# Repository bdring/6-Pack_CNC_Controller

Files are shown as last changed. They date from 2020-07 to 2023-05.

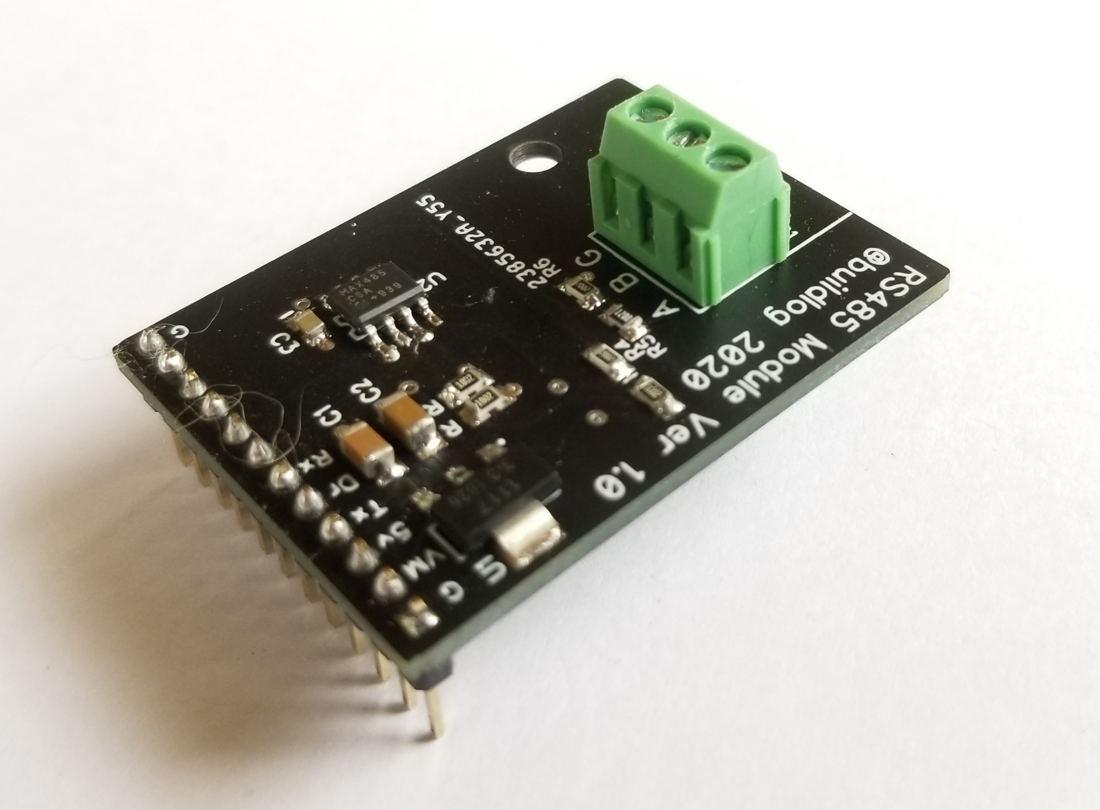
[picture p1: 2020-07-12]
images/20200711_132149.jpg

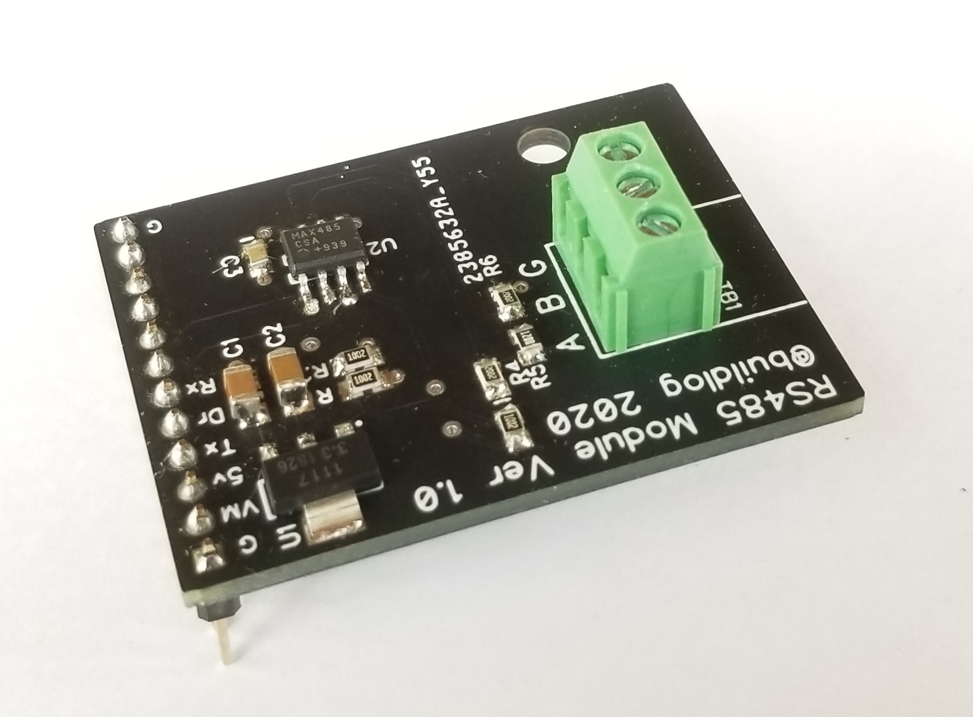
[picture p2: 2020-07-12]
images/20200711_133020.jpg

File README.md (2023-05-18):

# 6-Pack Grbl_ESP32 CNC Controller





### Overview

This is a fully modular CNC controller that runs Grbl_ESP32 firmware.

### Current Source Files.

The latest versions are [now on OSHLabs](https://oshwlab.com/bdring?tab=project&page=1) with the free version of EasyEDA. I did this to make it more accessible and easier to order.

### Features

- ESP32 Sockets to fit both narrow and wide 2 x 19 pin types.
- (6) Stepper Driver Outputs. These can be used for 6 axes (XYZABC) or any (2) can be ganged to allow dual motors on a single axis. These ganged motors can be controlled independently for axis squaring. It supports these types of drivers. Each driver has an independent enable/disable pin.
  - Standard Pololu/StepStick style driver modules.
  - Trinamic SPI type drivers. These are the ultra quiet types with sensorless endstop capability.
  - External Driver with 5V opto isolators.
(5) CNC I/O Modules. These interface with your machine. They include, but are not limited to, siwtch inputs, spindle control and accessory control. Currently there are (5) modules available.
  - High current AC/DC relay
  - 4x 5V Buffered output for lasers, PWM, spindle direction, spindle enable, ect.
  - RS485 Modbus Spindles
  - 0-10V Output Spindles
  - 4x Switch input with Optocouplers, filtering and Schmitt triggers. 
- SD Card Socket
- JTAG Programming/Debugging connector (or access to addition I/O pins

[](https://www.tindie.com/products/33366583/6-pack-universal-cnc-controller/)

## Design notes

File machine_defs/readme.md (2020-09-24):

These machine definitions are for reference only. They are not actively maintained, so they may not compile in future versions of Grbl_ESP32.

Machine definitions in the main Grbl_ESP32 repo are maintained and can be used as a reference to fix problems. You can also ask for help on Slack.

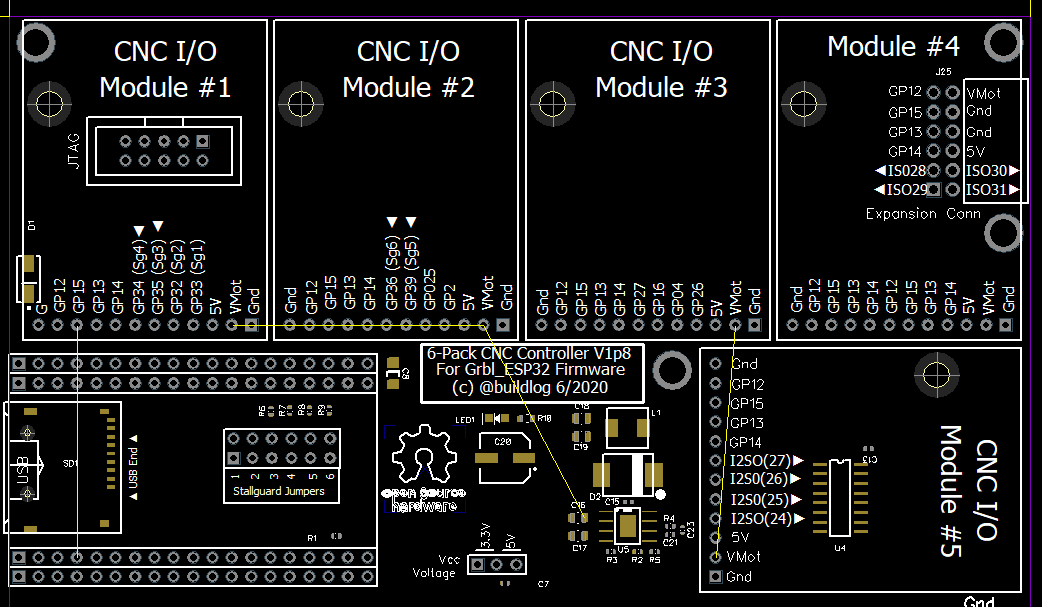
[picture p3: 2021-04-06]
images/expansion_port_pinout.png

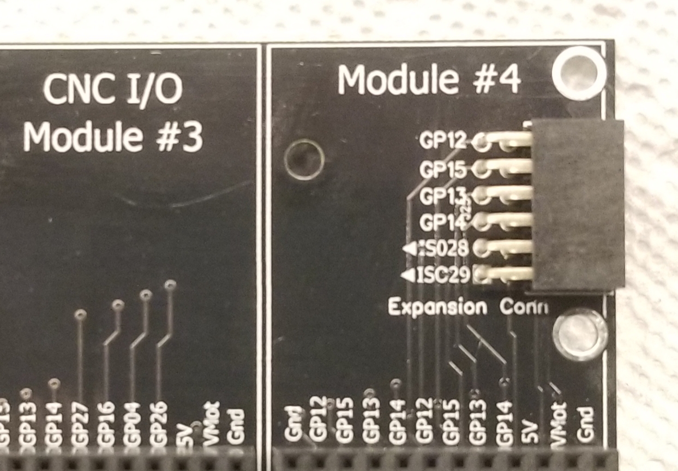
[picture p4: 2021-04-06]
images/6_pack_expansion.jpg

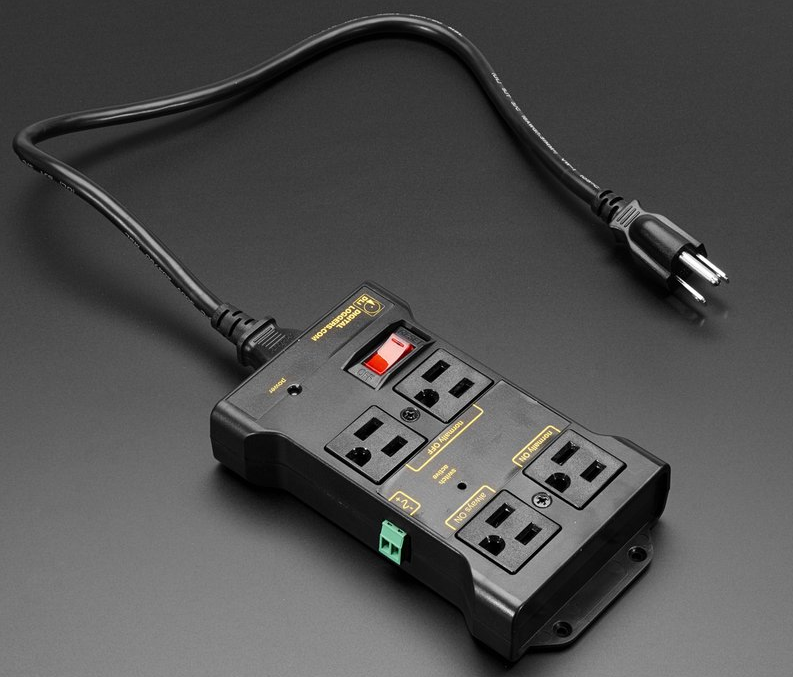
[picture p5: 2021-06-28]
images/iot_relay.png

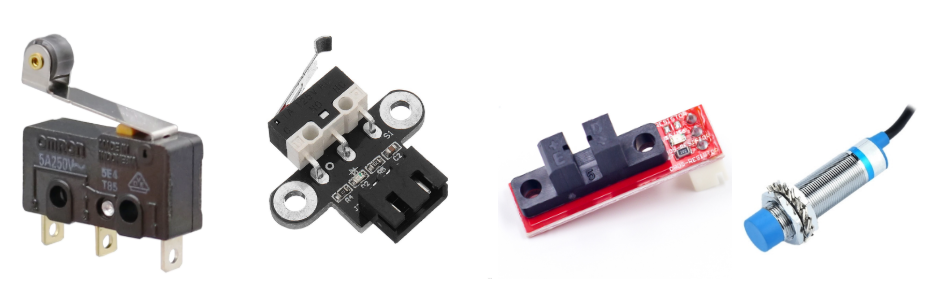
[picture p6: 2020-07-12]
images/switch_types.png

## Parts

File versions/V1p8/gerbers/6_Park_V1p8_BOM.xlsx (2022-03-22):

RefDes | Value | Name | Quantity | SMT | TH | Manufacturer | MFG P/N | Source
C1, C2, C3, C4, C5, C6, C7, C9, C11, C13, C15 | 100nF | NP_100nF_50V_0402 | 11 | 11 |  | Samsung Electro-Mechanics | CL05B104KB54PNC | https://lcsc.com/product-detail/Others_Samsung-Electro-Mechanics_CL05B104KB54PNC_Samsung-Electro-Mechanics-CL05B104KB54PNC_C307331.html
C8 | Do Not Place | NP_DNP_1206 |  |  |  | DNP | DN
C10, C12, C14, C22, C24, C25 | 330uF | POL_330uF_50V_10x10 | 6 | 6 |  | KS | UT1H331M1010VG | https://lcsc.com/product-detail/Aluminum-Electrolytic-Capacitors-SMD_KS-UT1H331M1010VG_C963258.html
C16, C17 | 2.2uF 50V | NP_2.2uF_50V_0805 | 2 | 2 |  | Guangdong Fenghua Advanced Tech | 0805F225M500NT | https://lcsc.com/product-detail/Multilayer-Ceramic-Capacitors-MLCC-SMD-SMT_FH-Guangdong-Fenghua-Advanced-Tech-0805F225M500NT_C49217.html
C18, C19 | 47uF 6.3V | NP_47uF_6.3V_0805 | 2 | 2 |  | Samsung Electro-Mechanics | CL21A476MQYNNNE | https://lcsc.com/product-detail/Multilayer-Ceramic-Capacitors-MLCC-SMD-SMT_SAMSUNG_CL21A476MQYNNNE_47uF-476-20-6-3V_C16780.html
C20 | 100uF 16V | POL_100uF_16V_6.3x5.4 | 1 | 1 |  | ROQANG | RT1C101M0605 | https://lcsc.com/product-detail/Aluminum-Electrolytic-Capacitors-SMD_ROQANG-RT1C101M0605_C267461.html
C21 | 39pF 50V | NP_39pF_50V_0402 | 1 | 1 |  | Yageo | CC0402JRNPO9BN390 | https://lcsc.com/product-detail/Multilayer-Ceramic-Capacitors-MLCC-SMD-SMT_39pF-390-5-50V_C106223.html/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
C23 | 6.8nF 50V | NP_6.8nF_50V_0402 | 1 | 1 |  | Guangdong Fenghua Advanced Tech | 0402B682K500NT | https://lcsc.com/product-detail/Multilayer-Ceramic-Capacitors-MLCC-SMD-SMT_6-8nF-682-10-50V_C1542.html
D1 | 40V 3A | Schottkey_40V_3A_DO-214AC | 1 | 1 |  | MDD（Microdiode Electronics） | B340A | https://lcsc.com/product-detail/Schottky-Barrier-Diodes-SBD_Jiangsu-Yutai-Elec-B340A_C64982.html
D2 | B560C | B560C | 1 | 1 |  | Diodes Incorporated | B560C-13-F | https://lcsc.com/product-detail/Schottky-Barrier-Diodes-SBD_Diodes-Incorporated-B560C-13-F_C85100.html
J1, J8, J12, J15, J19, J26 | 2 Pos | HDR Socket 1x2 0.1 | 6 |  | 6 | BOOMELE(Boom Precision Elec) | C49661 | https://lcsc.com/product-detail/Pin-Header-Female-Header_BOOMELE-Boom-Precision-Elec-C49661_C49661.html
J2, J3, J9, J10, J13, J14, J16, J17, J20, J21, J27, J28 | 8S | HDR Socket 1x8 0.1 | 12 |  | 12 | BOOMELE(Boom Precision Elec) | C27438 | https://lcsc.com/product-detail/Female-Header_2-54mm-1-8P-Straight-Female-header_C27438.html
J4, J5, J6, J7 | 19S | HDR Socket 1x19 0.1 | 4 |  | 4 | BOOMELE(Boom Precision Elec) | C319202 | https://lcsc.com/product-detail/Lack-of-specifications_BOOMELE-Boom-Precision-Elec-C319202_C319202.html
J11 | Do Not Place | DC3-10P
J18 | 6S | HDR Pin 2x6 0.1 | 1 |  | 1 | MINTRON | MTP125-1206S1 | https://lcsc.com/product-detail/Pin-Header-Female-Header_MINTRON-MTP125-1206S1_C358695.html
J22, J23, J24 | 3P | HDR Pin 1x3 0.1 | 3 |  | 3 | BOOMELE(Boom Precision Elec) | C49257 | https://lcsc.com/product-detail/Pin-Header-Female-Header_BOOMELE-Boom-Precision-Elec-C49257_C49257.html
J25 | Do Not Place | Header_2x6S_RA |  |  | 1
JP1, JP2, JP3, JP4 | 3P | Jumper_3p | 4 |  | 4 | BOOMELE(Boom Precision Elec) | C49257 | https://lcsc.com/product-detail/Pin-Header-Female-Header_BOOMELE-Boom-Precision-Elec-C49257_C49257.html
L1 | 10uH | 10uH_SMD_5.2x5.4 | 1 | 1 |  | Sunlord | MWSA0503S-100MT | https://lcsc.com/product-detail/Power-Inductors_Sunlord-MWSA0503S-100MT_C408412.html
LED1 | GRN | LED_GRN_0805 (Foshan) | 1 | 1 |  | Foshan NationStar Optoelectronics | NCD0805G1 | https://lcsc.com/product-detail/Light-Emitting-Diodes-LED_Foshan-NationStar-Optoelectronics-NCD0805G1_C84260.html
MH1, MH2, MH3, MH4, MH5, MH6 | Do Not Place | Mounting_hole_M3.7
MOD1, MOD2, MOD3, MOD4, MOD5 | 1x12 Socket | CNC_Module_Socket | 5 |  | 5 | CJT(Changjiang Connectors) | A2541HWV-12P | https://lcsc.com/product-detail/Pin-Header-Female-Header_CJT-Changjiang-Connectors-A2541HWV-12P_C225509.html
R1, R6, R7, R8, R9 | 10k | 10k_0402 | 5 | 5 |  | YAGEO | RC0402FR-0710KL | https://lcsc.com/product-detail/Chip-Resistor-Surface-Mount_YAGEO-RC0402FR-0710KL_C60490.html
R2 | 270k | 270k_0402 | 1 | 1 |  | Uniroyal Elec | 0402WGF2703TCE | https://lcsc.com/product-detail/Chip-Resistor-Surface-Mount_Uniroyal-Elec-0402WGF2703TCE_C25770.html/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
R3 | 100k | 100k_0402 | 1 | 1 |  | Uniroyal Elec | 0402WGF1003TCE | https://lcsc.com/product-detail/Chip-Resistor-Surface-Mount_Uniroyal-Elec-0402WGF1003TCE_C25741.html/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
R4 | 13k | 13k_0402 | 1 | 1 |  | Uniroyal Elec | 0402WGF1302TCE | https://lcsc.com/product-detail/Chip-Resistor-Surface-Mount_UNI-ROYAL-Uniroyal-Elec-0402WGF1302TCE_C25754.html
R5 | 51k | 51k_0402 | 1 | 1 |  | Uniroyal Elec | 0402WGF5102TCE | https://lcsc.com/product-detail/Chip-Resistor-Surface-Mount_Uniroyal-Elec-0402WGF5102TCE_C25794.html/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
R10 | 3.0k | 3.0k_0603 | 1 | 1 |  | YAGEO | RC0603FR-073KL | https://lcsc.com/product-detail/Chip-Resistor-Surface-Mount_3KR-3001-1_C126358.html
SD1 | Micro SD | TF-01A | 1 | 1 |  | Korean Hroparts Elec | TF-01A | https://lcsc.com/product-detail/Card-Sockets-Connectors_Korean-Hroparts-Elec-TF-01A_C91145.html
TB1, TB2, TB3, TB5, TB6, TB7 | 4 Pos | TB_3p5mm_4POS_KF2EDGR | 6 |  | 6 | Cixi Kefa Elec | KF2EDGR-3.5-4P | https://lcsc.com/product-detail/Pluggable-System-Terminal-Block_Cixi-Kefa-Elec-KF2EDGR-3-5-4P_C441173.html
TB4 | 2 Pos | TB_5mm_2POS Socket | 1 |  | 1 | Ningbo Xinlaiya Elec. | XY2500R-B-5.00-2P | https://lcsc.com/product-detail/Pluggable-System-Terminal-Block_Ningbo-Xinlaiya-Elec-XY2500R-B-5-00-2P_C505815.html
U1, U2, U3, U4 | 74AHCT595 | 74AHCT595 | 4 | 4 |  | Texas Instruments | SN74AHCT595DR | https://lcsc.com/product-detail/74-Series_Texas-Instruments_SN74AHCT595DR_Texas-Instruments-Texas-Instruments-SN74AHCT595DR_C133793.html
U5 | TPS54360 | TPS54360DDAR | 1 | 1 |  | Texas Instruments | TPS54360DDAR | https://lcsc.com/product-detail/DC-DC-Converters_Texas-Instruments-Texas-Instruments-TPS54360DDAR_C44377.html
 |  | Total parts | 86 | 44 | 43
 |  | Unique count | 29 | 20 | 10

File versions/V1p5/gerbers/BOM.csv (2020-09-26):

RefDes | Value | Name | Quantity | Manufacturer | MFG P/N
C1, C2, C3, C4, C5, C6, C7, C9, C11, C13, C16 | 100nF | NP_100nF_50V_0805 | 11 | KEMET | C0805C104K5RACAUTO
C8 | DNP | NP_DNP_1206 | 1 | DNP | DN
C10, C12, C15, C21, C23, C24 | 330uF | POL_330uF_50V_10x10 | 6 | Lelon | VZT331M1HTR-1010
C14, C19 | 10uF 35V | NP_10uF_35V_1206 | 2 | Taiyo Yuden | GMK316BJ106KL-T
C17 | 10uF | NP_10uF_50V_1206 | 1 | Taiyo Yuden | UMK316BBJ106ML-T
C18 | 100uF 16V | POL_100uF_16V_6.3x5.4 | 1 | PANASONIC | EEEHAC101WAP
C20 | 22uF | NP_22uF_6.3V_1206 | 1 | Taiyo Yuden | JMK316BJ226KL-T
C22 | 3.3nF | NP_3.3nF_50V_0603 | 1 | YAGEO | CS0603KRX7R9BB332
D1 | 40V 3A | Schottkey_40V_3A_DO-214AC | 1 | MDD(Microdiode Electronics) | B340A
J1, J8, J12, J15, J19, J25 |  | HDR Socket 1x2 0.1 | 6 | BOOMELE(Boom Precision Elec) | C49661
J2, J3, J9, J10, J13, J14, J16, J17, J20, J21, J26, J27 |  | HDR Socket 1x8 0.1 | 12 | BOOMELE(Boom Precision Elec) | C27438
J4, J5, J6, J7 |  | HDR Socket 1x19 0.1 | 4 | Popular Products About LCSC | C319202
J11 | JTAG | DC3-10P | 1
J18 |  | HDR Pin 2x6 0.1 | 1 | MINTRON | MTP125-1206S1
J22, J23, J24 |  | HDR Pin 1x3 0.1 | 3 | BOOMELE(Boom Precision Elec) | C49257
JP1, JP2, JP3, JP4 |  | Jumper_3p | 4 | BOOMELE(Boom Precision Elec) | C49257
L1 | 5.6uH | 5.6uH_SMD_10.0_11.5 | 1 | COILMX | MS1040-5R6M
LED1 | GRN | LED_GRN_0805 (Foshan) | 1 | Foshan NationStar Optoelectronics | NCD0805G1
MH1, MH2, MH3, MH4 |  | Mounting_hole_M3.7 | 4
MOD1, MOD2, MOD3, MOD4, MOD5 | 1x12 Socket | CNC_Module_Socket | 5 | CJT(Changjiang Connectors) | A2541HWV-12P
R1 | 115k | 115K_0603 | 1 | YAGEO | RC0603FR-07115KL
R2 | 22.1k | 22.1k_0603 | 1 | YAGEO | RC0603FR-0722K1L
R3 | 200k | 200k_0603 | 1 | YAGEO | RC0603FR-07200KL
R4 | 42.1k | 41.2k_0603 | 1 | YAGEO | RC0603FR-0741K2L
R5, R6, R7, R8 | 10k | 10k_0805 | 4 | YAGEO | RC0805FR-0710KL
R9 | 3.0k | 3.0k_0805 | 1 | YAGEO | RC0805FR-073KL
SD1 | Micro SD | TF-01A | 1 | Korean Hroparts Elec | TF-01A
TB1, TB2, TB3, TB5, TB6, TB7 | 4 Pos | TB_3.5mm_4POS_PHOENIX_1945119 | 6 | Phoenix contact | 1945119 (Mate is 1984183)
TB4 | 2 Pos | TB_5mm_2POS Socket | 1 | Ningbo Xinlaiya Elec. | XY2500R-B-5.00-2P (Mate is XY2500F-A-5.0-2P)
U1, U2, U3, U4 | 74AHCT595 | 74AHCT595 | 4 | Nexperia | 74AHCT595D,118
U5 | AP64350SP-13 | AP64350 | 1 | Diodes Inc | AP64350SP-13

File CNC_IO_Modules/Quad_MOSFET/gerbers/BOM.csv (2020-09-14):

RefDes | Value | Name | Quantity | Manufacturer | MFG P/N
LED1, LED2, LED3, LED4 | GRN | LED_GRN_0805 | 4 | Lite-On | LTST-C170KGKT
MOD1 | 1x12 P | CNC_Module_Pins | 1 | CJT(Changjiang Connectors) | A2541WV-12P
Q1, Q2, Q3, Q4 | 42V 10A | NCV8403A | 4 | On Semiconductor | NCV8403A
R1, R2, R3, R4 | 300R | 300R_0603 | 4 | YAGEO | RC0603FR-07330RL
R5 | 10R | 10R_0805 | 1 | YAGEO | RC0805FR-0710RL
TB1 | 8 Pos | TB_3p5mm_8POS_PHOENIX_1945151 | 1 | Phoenix contact | 1945151
TB2 | 2 Pos | TB_3.5mm_2POS_SOCKET_VERT | 1 | Ningbo Xinlaiya Elec | XY2500R-B-5.00-2P

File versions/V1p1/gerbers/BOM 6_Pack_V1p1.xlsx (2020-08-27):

RefDes | Quantity | Qty SMT | Qty TH | Name | Value | Manufacturer | Mfg P/N | Source
C1, C2 | 2 | 2 |  | Capacitor 1206 | 10uF | Taiyo Yuden | GMK316BJ106KL-T | https://lcsc.com/product-detail/Multilayer-Ceramic-Capacitors-MLCC-SMD-SMT_Taiyo-Yuden-GMK316BJ106KL-T_C92797.html
C3, C6, C7, C13, C14, C23, C24, C25, C26, C27, C28 | 11 | 11 |  | Capacitor 0805 | 100nF | Kemet | C0805C104K5RACAUTO | https://lcsc.com/product-detail/Multilayer-Ceramic-Capacitors-MLCC-SMD-SMT_KEMET_C0805C104K5RACAUTO_100nF-104-10-50V-Car-level_C129641.html
C4 | 1 | 1 |  | Capacitor 0805 | 150pF | CCTC | TCC0805X7R151K500BT | https://lcsc.com/product-detail/Multilayer-Ceramic-Capacitors-MLCC-SMD-SMT_CCTC-TCC0805X7R151K500BT_C282743.html
C5, C9 | 2 | 2 |  | Capacitor 1206 | 22uF 6.3V | Taiyo Yuden | JMK316BJ226KL-T | https://lcsc.com/product-detail/Multilayer-Ceramic-Capacitors-MLCC-SMD-SMT_TAIYO-YUDEN_JMK316BJ226KL-T_22uF-226-10-6-3V_C92791.html
C8 | 1 | 1 |  | Capacitor, Electrolytic | 100u 16V | Panasonic | EEEHAC101WAP | https://lcsc.com/product-detail/Aluminum-Electrolytic-Capacitors-SMD_PANASONIC-EEEHAC101WAP_C336467.html
C17, C18, C19, C20, C21, C22 | 6 | 6 |  | Capacitor, Electrolytic | 330uF 50V | Lelon | VZT331M1HTR-1010 | https://lcsc.com/product-detail/Others_Lelon-VZT331M1H1010-TRO_C249985.html
D1, D2 | 2 | 2 |  | Diode, Schottkey 3A DO-214AC | 3A | (MDD) Jiangsu Yutai Elec | C64982 | https://lcsc.com/product-detail/Schottky-Barrier-Diodes-SBD_Jiangsu-Yutai-Elec-B340A_C64982.html
J1, J3, J6,J9 | 4 |  | 4 | 1x19 Female Header 0.1 |  | AliExpress |  | https://www.aliexpress.com/item/100Pcs-Per-Lot-2-54mm-Pitch-1x19-Pin-19-Pin-Female-Single-Row-Straight-Header-Strip/32760221364.html
J4, J5, J8, JP1, JP2, JP3, JP4 | 7 |  | 7 | Header, Male 1x3 0.1 | 1x3 | Boom Precision Elec | C49257 | https://lcsc.com/product-detail/Pin-Header-Female-Header_BOOMELE-Boom-Precision-Elec-C49257_C49257.html
J12 | 1 |  | 1 | Header, Male 2x6 | 2x6 | MINTRON | MTP125-1206S1 | https://lcsc.com/product-detail/Pin-Header-Female-Header_MINTRON-MTP125-1206S1_C358695.html
J14, J15, J16, J17, J18, J19, J26, J27, J28, J29, J30, J31 | 12 |  | 12 | Header, Female 1x8 | 1x8 | BOOMELE(Boom Precision Elec) | C27438 | https://lcsc.com/product-detail/Female-Header_2-54mm-1-8P-Straight-Female-header_C27438.html
J20, J21, J22, J23, J24, J25 | 6 |  | 6 | Header, Female 1x2 | 1x2 | BOOMELE(Boom Precision Elec) | C49661 | https://lcsc.com/product-detail/Pin-Header-Female-Header_BOOMELE-Boom-Precision-Elec-C49661_C49661.html
J33 | 0 |  |  | Do not place
L1 | 1 | 1 |  | Inductor | 4.7uH | Chilisin Elec | MHCI06030-4R7M-R8 | https://lcsc.com/product-detail/Power-Inductors_Chilisin-Elec-MHCI06030-4R7M-R8_C108295.html
LED1 | 1 | 1 |  | LED Clear Green 0805 |  | Foshan NationStar Optoelectronics | NCD0805G1 | https://lcsc.com/product-detail/Light-Emitting-Diodes-LED_Emerald-SMDLED-Iv-220-270mcd-atIF-5mA_C84260.html
MOD1, MOD2, MOD3, MOD4, MOD5 | 5 |  | 5 | Header, Feamle 1x12 | 1x12 | HOAUC | 2685Y-112CNG1SNA01 | https://lcsc.com/product-detail/Pin-Header-Female-Header_HOAUC-2685Y-112CNG1SNA01_C350303.html
R1, R2 | 2 | 2 |  | RES_0805 | 100k | YAGEO | AC0805FR-07100KL | https://lcsc.com/product-detail/Chip-Resistor-Surface-Mount_100KR-1003-1_C144587.html
R3 | 1 | 1 |  | RES_0805 | 40.2k | YAGEO | AC0805FR-0740K2L | https://lcsc.com/product-detail/Others_YAGEO-AC0805FR-0740K2L_C228820.html
R4 | 1 | 1 |  | RES_0805 | 210k | YAGEO | AC0805FR-07210KL | https://lcsc.com/product-detail/Others_YAGEO-AC0805FR-07210KL_C228629.html
R5, R6, R7, R8 | 4 | 4 |  | RES_0805 | 10k | YAGEO | AC0805FR-0710KL | https://lcsc.com/product-detail/Chip-Resistor-Surface-Mount_10KR-1002-1_C140868.html
R10 | 1 | 1 |  | RES_0805 | 300R | YAGEO | RC0805FR-07300RL | https://lcsc.com/product-detail/Chip-Resistor-Surface-Mount_300R-300R-1_C114529.html
SD1 | 1 | 1 |  | TF-01A |  | Korean Hroparts Elec TF-01A | TF-01A | https://lcsc.com/product-detail/Connector-Card-Sockets_Korean-Hroparts-Elec-TF-01A_C91145.html
TB1 | 1 |  | 1 | 2 Pos Terminal Block |  | Ningbo Xinlaiya Elec. | XY2500R-B-5.00-2P | https://lcsc.com/product-detail/Pluggable-System-Terminal-Block_Ningbo-Xinlaiya-Elec-XY2500R-B-5-00-2P_C505815.html
TB2, TB3, TB4, TB5, TB6, TB7 | 0 |  |  | 4 Pos Terminal Block |  | Phoenix Contact | 1945119 | https://www.mouser.com/ProductDetail/Phoenix-Contact/1945119?qs=BYlwlsDsB%2FoxVFDUDE1oIQ%3D%3D
U1 | 1 | 1 |  | Power Supply, Buck 3A | 3A | Monolithic Power Systems | MP1584EN-LF-Z | https://lcsc.com/product-detail/DC-DC-Converters_MPS_MP1584EN-LF-Z_MP1584EN-LF-Z_C15051.html
U2, U3, U4, U5 | 4 | 4 |  | 74AHCT595 | 74AHCT595 | Nexperia | 74AHCT595D,118 | https://www.mouser.com/ProductDetail/Nexperia/74AHCT595D118?qs=P62ublwmbi%2FjQEpjzH34Ig%3D%3D
Totals | 65 | 29 | 36

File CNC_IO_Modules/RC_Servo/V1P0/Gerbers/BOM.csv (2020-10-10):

RefDes | Value | Name | Quantity | Manufacturer | MFG P/N | Source
J1, J2, J3, J4 | 1x3 | HDR Pin 1x3 0.1 | 4 | BOOMELE(Boom Precision Elec) | C49257 | https://lcsc.com/product-detail/Pin-Header-Female-Header_BOOMELE-Boom-Precision-Elec-C49257_C49257.html
MOD1 | 1x12 P | CNC_Module_Pins | 1 | CJT(Changjiang Connectors) | A2541WV-12P | https://lcsc.com/product-detail/Pin-Header-Female-Header_CJT-Changjiang-Connectors-A2541WV-12P_C225487.html
S1 | SPDT | XKB_SS-12D11L5 | 1 | XKB Connectivity | SS-12D11L5 | https://lcsc.com/product-detail/Toggle-Switches_XKB-Connectivity-SS-12D11L5_C319010.html
TB4 | 2 Pos | TB_5mm_2POS Socket | 1 | Ningbo Xinlaiya Elec. | XY2500R-B-5.00-2P | https://lcsc.com/product-detail/Pluggable-System-Terminal-Block_Ningbo-Xinlaiya-Elec-XY2500R-B-5-00-2P_C505815.html

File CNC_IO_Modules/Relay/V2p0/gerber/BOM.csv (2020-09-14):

RefDes | Value | Name | Quantity | Manufacturer | MFG P/N | Source
D1 |  | Schottkey_40V_3A_DO-214AC | 1 | MDD(Microdiode Electronics) | B340A | https://lcsc.com/product-detail/Schottky-Barrier-Diodes-SBD_Jiangsu-Yutai-Elec-B340A_C64982.html
K1 | 5VDC | Relay_SRD-05VDC-SL-C | 1 |  | SRD-05VDC-SL-C | https://lcsc.com/product-detail/Relays_Ningbo-Songle-Relay-SRD-05VDC-SL-C_C35449.html
LED1 | GRN | LED_GRN_0805 (Foshan) | 1 | Foshan NationStar Optoelectronics | NCD0805G1 | https://lcsc.com/product-detail/Light-Emitting-Diodes-LED_Foshan-NationStar-Optoelectronics-NCD0805G1_C84260.html
MOD1 | 1x12 P | CNC_Module_Pins | 1 | CJT(Changjiang Connectors) | A2541WV-12P | https://lcsc.com/product-detail/Pin-Header-Female-Header_CJT-Changjiang-Connectors-A2541WV-12P_C225487.html
Q1 | NPN 100mA 45V | MMBT9014B | 1 | ST(Semtech) | MMBT9014B | https://lcsc.com/product-detail/Transistors-NPN-PNP_ST-Semtech-MMBT9014B_C109430.html
R1 | 1.0k | 1.0k_0805 | 1 | YAGEO | RC0805FR-071K5L | https://lcsc.com/product-detail/Chip-Resistor-Surface-Mount_YAGEO-RC0805FR-071KL_C95781.html
R2 | 1.5k | 1.5k_0805 | 1 | YAGEO | RC0805FR-071K5L | https://lcsc.com/product-detail/Chip-Resistor-Surface-Mount_1-5KR-1501-1_C114555.html
TB2 |  | TB_5mm_3POS | 1 | JILN

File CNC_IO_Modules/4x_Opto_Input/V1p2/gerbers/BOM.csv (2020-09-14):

RefDes | Value | Name | Quantity | Manufacturer | MFG P/N
C1, C2 | 1uF | NP_1uF_50V_0805 | 2 | CCTC | TCC0805X7R105K500DTB
C3 | 2.2uF | NP_2.2uF_16V_0805 | 1 | Samsung Electro-Mechanics | CL21B225KOFNNNE
C4, C5, C6, C7, C8 | 100nF | NP_100nF_50V_0603 | 5 | KEMET | C0603C104K5RACTU
MOD1 |  | CNC_Module | 1 | CJT(Changjiang Connectors) | A2541WV-12P
OPT1 | TP521-4 | TLP521-4 | 1 | Isocom Components | TLP521-4GBSM
PS1 | 5V | B0505S-1WR3 | 1 | MORNSUN Guangzhou S&T | B0505S-1WR3
PS2 | 3.3V | LDO_3V3_150mA_SOT-89 | 1 | Diodes Incorporated | AP2204RA-3.3TRG1
R1, R2, R3, R4 | 300R | 300R_0603 | 4 | YAGEO | RC0603FR-07330RL
R5, R6, R7, R8 | 10k | 10k_0603 | 4 | YAGEO | RC0603FR-0710KL
R9, R10, R11, R12, R13 | 220R | 220R_0603 | 5 | YAGEO | RC0603FR-07220RL
TB1, TB2 |  | KL128H-3.5_3x2 | 2 | KEFA | KF128A-3.5 3P
U2 |  | SN74AC14D | 1 | Texas Instruments | SN74HC14PWR

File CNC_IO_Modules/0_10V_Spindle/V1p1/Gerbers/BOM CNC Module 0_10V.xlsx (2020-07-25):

RefDes | Quantity | Qty SMT | Qty TH | Value | Name | Pattern | Manufacturer | MFG P/N | Source | Alt Source
C1, C2 | 1 | 1 |  | 100nF | CAP_0805 | CAP_0805 | Kemet | C0805C104K5RACAUTO | https://lcsc.com/product-detail/Multilayer-Ceramic-Capacitors-MLCC-SMD-SMT_KEMET_C0805C104K5RACAUTO_100nF-104-10-50V-Car-level_C129641.html
LED1, LED2, LED3, LED4 | 4 | 4 |  | Green | LED Green Clear | 805 | Lite-On | LTST-C170KGKT | https://lcsc.com/product-detail/Light-Emitting-Diodes-LED_Lite-On-LTST-C170KGKT_C98221.html
MOD1 | 1 |  | 0 | Do not place
OPT1, OPT2 | 2 | 2 |  | Opto | Opto | SMD4 | Everlight Elec | EL817S1(D)(TU)-F | https://lcsc.com/product-detail/Optocouplers_Everlight-Elec-EL817S1-D-TU-F_C108319.html
R1, R2, R3, R4, R5 | 5 | 5 |  | 300R | Resistor 300R 1% |  | YAGEO | AC0805FR-07300RL | https://lcsc.com/product-detail/_AC0805FR-07300RL_C144566.html
R6, R9, R10 | 4 | 4 |  | 10k | Resistor 10k 1% | RES_0805 | YAGEO | AC0805FR-0710KL | https://lcsc.com/product-detail/Chip-Resistor-Surface-Mount_10KR-1002-1_C140868.html
R7 | 1 | 1 |  | 20k | Pot 20K SMT | Pot | HDK(Hokuriku Elec Industry) | VG039NCHXTB203 | https://lcsc.com/product-detail/Variable-Resistors_HDK-Hokuriku-Elec-Industry-VG039NCHXTB203_C128550.html
R8 | 1 | 1 |  | 4.99K | Resistor 4.99K 1% 0805 | 805 | YAGEO | AC0805FR-074K99L | https://lcsc.com/product-detail/Others_YAGEO-AC0805FR-074K99L_C228871.html
TB1 | 1 |  | 0 | Do Not Place
U1 | 1 | 1 |  | LM358P | LM358 | SOIC-8 | STMicroelectronics | LM358ADT | https://lcsc.com/product-detail/General-Purpose-Amplifiers_STMicroelectronics-LM358ADT_C92457.html
Total |  | 19

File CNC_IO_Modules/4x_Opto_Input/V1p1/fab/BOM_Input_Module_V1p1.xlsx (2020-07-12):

RefDes | Quantity | Qty SMT | Qty TH | Value | Name | Pattern | Manufacturer | Mfg P/N | Source
C1, C2 | 2 | 2 |  | 1uF | Capacitor 0805 1uF 50V 20% | CAP_0805 | CCTC | TCC0805X7R105K500DTB | https://lcsc.com/product-detail/Multilayer-Ceramic-Capacitors-MLCC-SMD-SMT_CCTC-TCC0805X7R105K500DTB_C282736.html
C3 | 1 | 1 |  | 2.2uF | Capacitor 0805 | CAP_0805 | Samsung Electro-Mechanics | CL21B225KOFNNNE | https://lcsc.com/product-detail/Multilayer-Ceramic-Capacitors-MLCC-SMD-SMT_SAMSUNG_CL21B225KOFNNNE_2-2uF-225-10-16V_C28234.html
C4, C5, C6, C7, C8 | 4 | 4 |  | 100nF | Capacitor 0603 | CAP_0603 | Walsin Tech Corp | 0603F104Z250 | https://lcsc.com/product-detail/Multilayer-Ceramic-Capacitors-MLCC-SMD-SMT_Walsin-Tech-Corp-0603F104Z250_C125841.html
MOD1 | 0 |  |  |  | Header, Male 1x12 0.1" | Do Not Place
OPT1 | 1 | 1 |  | TP521-4 | Optocoupler | TLP521-4SM | Isocom Components | TLP521-4GBSM | https://lcsc.com/product-detail/Optocouplers_Isocom-Components-TLP521-4GBSM_C191332.html
PS1 | 1 |  | 0 | 5V | Isloated P/S 5V/5V | Do Not Place
PS2 | 1 | 1 |  |  | LDO 5V | SOT89 | Diodes Incorporated | AP2204RA-3.3TRG1 | https://lcsc.com/product-detail/Low-Dropout-Regulators-LDO_Diodes-Incorporated-AP2204RA-3-3TRG1_C151625.html
R1, R2, R3, R4 | 4 | 4 |  | 300 | Resitor 0603 | RES_0603 | LIZ Elec | CR0603JA0301G | https://lcsc.com/product-detail/Chip-Resistor-Surface-Mount_LIZ-Elec-CR0603JA0301G_C101323.html
R5, R6, R7, R8 | 4 | 4 |  | 10k | Resitor 0603 | RES_0603 | YAGEO | RC0603FR-0710KL | https://lcsc.com/product-detail/Chip-Resistor-Surface-Mount_10KR-1002-1_C98220.html
R9, R10, R11, R12, R13 | 5 | 5 |  | 220 | Resitor 0603 | RES_0805 | YAGEO | RC0603FR-07220RL | https://lcsc.com/product-detail/Chip-Resistor-Surface-Mount_220R-220R-1_C107696.html
TB1, TB3 | 0 |  | 0 |  | Do not place | Do not place
TB2, TB4 | 0 |  | 0 |  | Do not place | Do not place
U2 | 1 | 1 |  |  | Schmitt Trigger SN74AC14D | TSSOP-14 | Texas Instruments | SN74HC14PWR | https://lcsc.com/product-detail/Gates-and-Inverters_Texas-Instruments_SN74HC14PWR_Texas-Instruments-Texas-Instruments-SN74HC14PWR_C6821.html
 |  | 23

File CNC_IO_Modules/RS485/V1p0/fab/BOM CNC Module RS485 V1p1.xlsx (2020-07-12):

RefDes | Quantity | Qty SMT | Qty TH | Value | Name | Pattern | Manufacturer | MFG P/N | Source
C1 | 1 | 1 |  | 10uF | CAP_NP_1206 | CAP_1206 | Taiyo Yuden | GMK316BJ106KL-T | https://lcsc.com/product-detail/Multilayer-Ceramic-Capacitors-MLCC-SMD-SMT_Taiyo-Yuden-GMK316BJ106KL-T_C92797.html
C2 | 1 | 1 |  | 22uF |  | CAP_1206 | Taiyo Yuden | JMK316BJ226KL-T | https://lcsc.com/product-detail/Multilayer-Ceramic-Capacitors-MLCC-SMD-SMT_TAIYO-YUDEN_JMK316BJ226KL-T_22uF-226-10-6-3V_C92791.html
C3 | 1 | 1 |  | 100nF | CAP_0805 | CAP_0805 | Kemet | C0805C104K5RACAUTO | https://lcsc.com/product-detail/Multilayer-Ceramic-Capacitors-MLCC-SMD-SMT_KEMET_C0805C104K5RACAUTO_100nF-104-10-50V-Car-level_C129641.html
MOD1 | 1 |  | 0 |  | Do not place
R1, R2, R3 | 3 | 3 |  | 10k | RES_0805 | RES_0805 | YAGEO | AC0805FR-0710KL | https://lcsc.com/product-detail/Chip-Resistor-Surface-Mount_10KR-1002-1_C140868.html
R4, R6 | 2 | 2 |  | 20k | RES_0805 | RES_0805 | YAGEO | RC0805FR-0720KL | https://lcsc.com/product-detail/Chip-Resistor-Surface-Mount_20KR-2002-1_C114566.html
R5 | 1 | 1 |  | 120 | RES_0805 | RES_0805 | YAGEO | RC0805FR-07120RL | https://lcsc.com/product-detail/Chip-Resistor-Surface-Mount_120R-120R-1_C114245.html
TB1 | 1 |  | 0 |  | Do Not Place
U1 | 1 | 1 |  | 3.3V | AMS1117 | SOT223-4 | Advanced Monolithic Systems | AMS1117-3.3 | https://lcsc.com/product-detail/Low-Dropout-Regulators-LDO_AMS_AMS1117-3-3_AMS1117-3-3_C6186.html
U2 | 1 | 1 |  |  | MAX485CSA | SOIC-8/150mil | Maxim Integrated | MAX3485ESA+T | https://lcsc.com/product-detail/RS-485-RS-422-ICs_Maxim-Integrated_MAX3485ESA-T_Maxim-Integrated-MAX3485ESA-T_C18148.html
Total |  | 11

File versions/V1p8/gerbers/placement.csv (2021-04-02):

RefDes | Origin X (mm) | Origin Y (mm) | Side | Rotate
C1 | 39.85 | 60.173 | Top | 0.0
C2 | 30.111 | 60.649 | Top | 0.0
C3 | 51.701 | 60.649 | Top | 0.0
C4 | 70.751 | 60.649 | Top | 0.0
C5 | 92.341 | 60.649 | Top | 0.0
C6 | 110.099 | 60.649 | Top | 0.0
C7 | 74.995 | 67.634 | Top | 180.0
C8 | 60.332 | 95.098 | Top | 270.0
C9 | 78.585 | 60.173 | Top | 0.0
C10 | 26.518 | 53.243 | Top | 90.0
C11 | 116.368 | 60.173 | Top | 0.0
C12 | 48.108 | 53.243 | Top | 90.0
C13 | 122.72 | 85.256 | Top | 0.0
C14 | 67.158 | 53.243 | Top | 90.0
C15 | 91.193 | 78.271 | Top | 0.0
C16 | 84.621 | 76.207 | Top | 0.0
C17 | 84.621 | 73.825 | Top | 0.0
C18 | 85.097 | 89.224 | Top | 0.0
C19 | 85.097 | 86.843 | Top | 0.0
C20 | 75.095 | 83.985 | Top | 180.0
C21 | 96.686 | 73.984 | Top | 180.0
C22 | 88.748 | 53.243 | Top | 90.0
C23 | 98.273 | 74.619 | Top | 90.0
C24 | 106.528 | 53.243 | Top | 90.0
C25 | 127.642 | 53.243 | Top | 90.0
D1 | 12.548 | 107.48 | Top | 90.0
D2 | 91.193 | 81.763 | Top | 180.0
J1 | 22.708 | 44.298 | Top | 180.0
J2 | 18.898 | 35.408 | Top | 270.0
J3 | 31.598 | 35.408 | Top | 270.0
J4 | 34.138 | 96.368 | Top | 0.0
J5 | 34.138 | 93.828 | Top | 0.0
J6 | 34.138 | 68.428 | Top | 0.0
J7 | 34.138 | 70.968 | Top | 0.0
J8 | 43.028 | 44.298 | Top | 180.0
J9 | 39.218 | 35.408 | Top | 270.0
J10 | 51.918 | 35.408 | Top | 270.0
J11 | 30.328 | 124.308 | Top | 180.0
J12 | 63.348 | 44.298 | Top | 180.0
J13 | 59.538 | 35.408 | Top | 270.0
J14 | 72.238 | 35.408 | Top | 270.0
J15 | 83.668 | 44.298 | Top | 180.0
J16 | 79.858 | 35.408 | Top | 270.0
J17 | 92.558 | 35.408 | Top | 270.0
J18 | 45.758 | 85.258 | Top | 0.0
J19 | 103.988 | 44.298 | Top | 180.0
J20 | 100.178 | 35.408 | Top | 270.0
J21 | 112.878 | 35.408 | Top | 270.0
J22 | 73.984 | 70.016 | Top | 0.0
J23 | 138.913 | 34.773 | Top | 270.0
J24 | 12.866 | 46.044 | Top | 270.0
J25 | 132.563 | 125.578 | Top | 90.0
J26 | 124.308 | 44.298 | Top | 180.0
J27 | 120.498 | 35.408 | Top | 270.0
J28 | 133.198 | 35.408 | Top | 270.0
JP1 | 18.898 | 56.363 | Top | 90.0
JP2 | 13.818 | 56.363 | Top | 90.0
JP3 | 12.866 | 26.042 | Top | 90.0
JP4 | 16.358 | 56.363 | Top | 90.0
L1 | 91.129 | 87.954 | Top | 180.0
LED1 | 73.984 | 89.224 | Top | 180.0
MOD1 | 27.788 | 101.448 | Top | 180.0
MOD2 | 60.808 | 101.448 | Top | 180.0
MOD3 | 93.828 | 101.448 | Top | 180.0
MOD4 | 126.757 | 101.448 | Top | 180.0
MOD5 | 102.718 | 82.398 | Top | 90.0
R1 | 52.871 | 73.825 | Top | 0.0
R2 | 92.399 | 71.762 | Top | 180.0
R3 | 88.907 | 71.762 | Top | 180.0
R4 | 96.686 | 75.102 | Top | 180.0
R5 | 94.622 | 71.762 | Top | 180.0
R6 | 44.298 | 90.177 | Top | 90.0
R7 | 46.758 | 90.258 | Top | 90.0
R8 | 49.349 | 90.258 | Top | 90.0
R9 | 51.918 | 90.336 | Top | 90.0
R10 | 77.852 | 89.224 | Top | 180.0
SD1 | 17.008 | 82.773 | Top | 0.0
TB1 | 25.416 | 17.628 | Top | 0.0
TB2 | 45.736 | 17.628 | Top | 0.0
TB3 | 66.056 | 17.628 | Top | 0.0
TB4 | 138.278 | 55.887 | Top | 90.0
TB5 | 86.376 | 17.628 | Top | 0.0
TB6 | 106.696 | 17.628 | Top | 0.0
TB7 | 127.016 | 17.628 | Top | 0.0
U1 | 38.108 | 54.141 | Top | 0.0
U2 | 78.748 | 54.141 | Top | 0.0
U3 | 117.483 | 54.141 | Top | 0.0
U4 | 119.069 | 78.747 | Top | 0.0
U5 | 91.193 | 75.091 | Top | 270.0

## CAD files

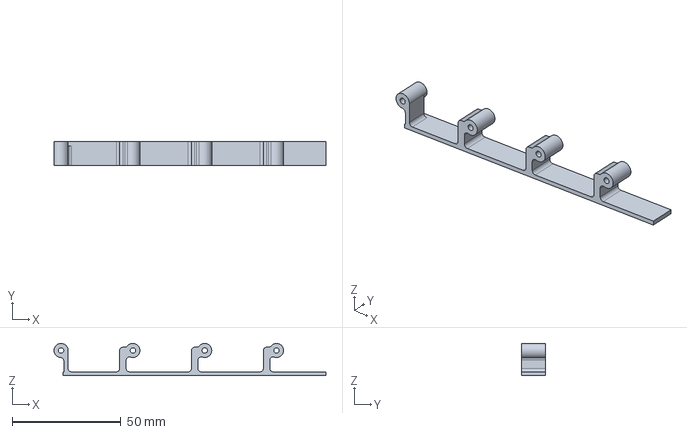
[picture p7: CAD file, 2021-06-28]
3D_Files/4x_support.stp
125.1 x 11.0 x 14.8 mm

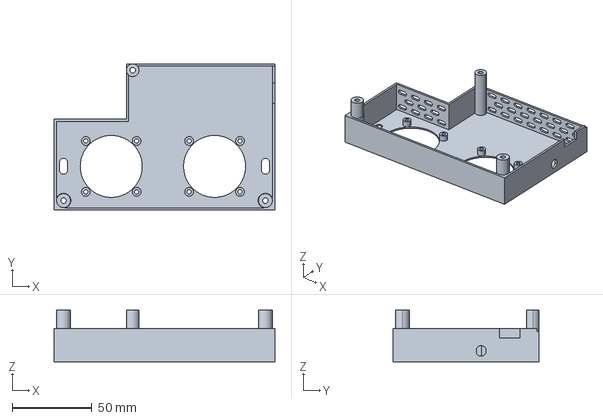
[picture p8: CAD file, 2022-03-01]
3D_Files/case/6_pack_cover_top.stp
139.0 x 92.0 x 32.7 mm

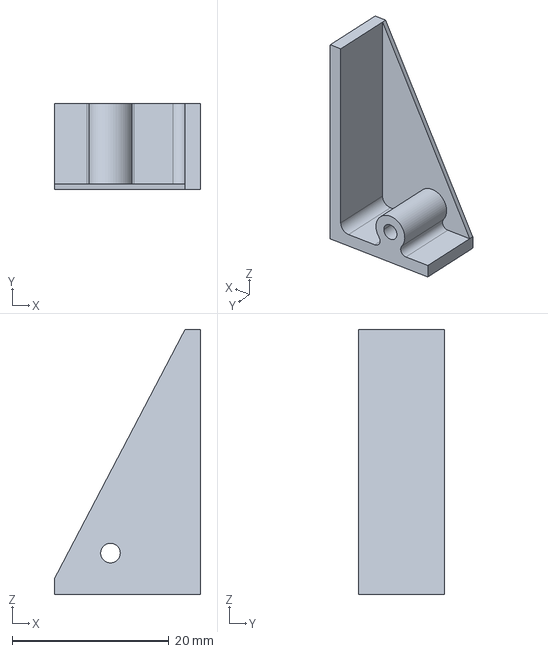
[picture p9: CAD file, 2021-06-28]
3D_Files/1x_supp.stp
18.7 x 11.0 x 33.8 mm

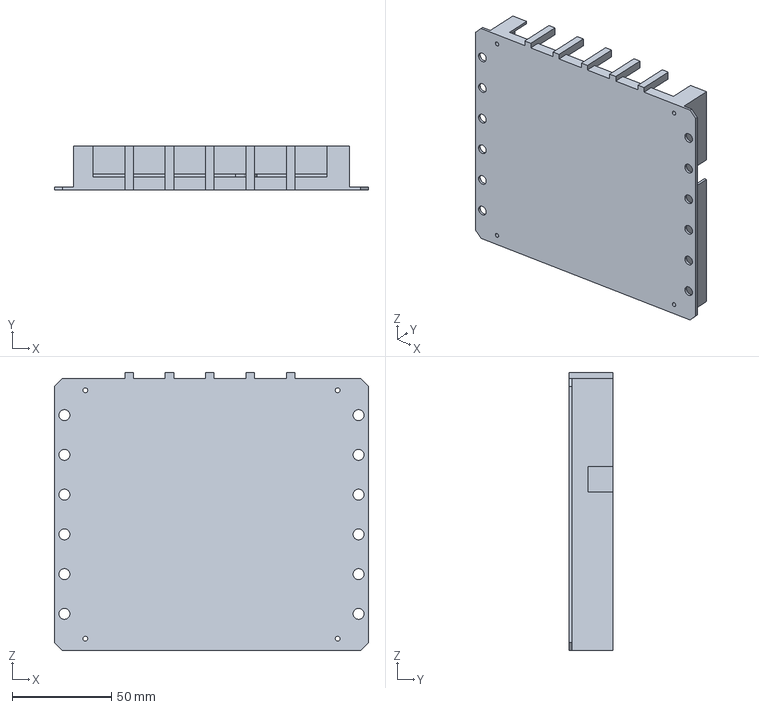
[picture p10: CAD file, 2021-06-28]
3D_Files/case/6_pack_case_bottom.stp
158.0 x 22.2 x 140.0 mm

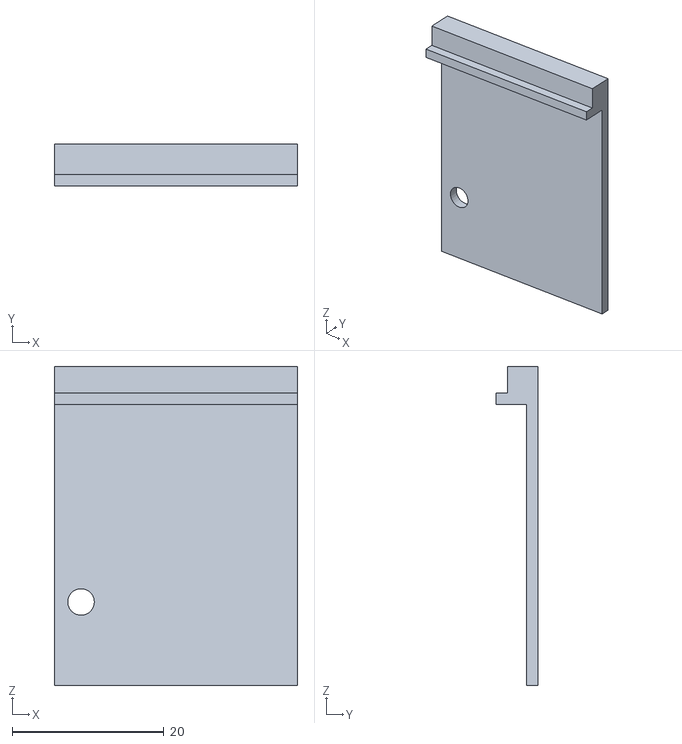
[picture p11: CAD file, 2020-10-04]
3D_Files/case/dummy_module.stl
32.0 x 5.50 x 42.0

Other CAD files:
3D_Files/1x_supp.stl
3D_Files/4x_support.stl
3D_Files/case/6_pack_case_bottom.stl
3D_Files/case/6_pack_cover_top.stl

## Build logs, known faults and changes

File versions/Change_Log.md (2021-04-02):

## 6 Pack CNC Controller PCB Change Log

### V1.8

-  Changed the power supply to the latest chip I have been using that is usually available on JLC. TI p/n TPS54360 LCSC P/N C44377
- Added an expansion port on the upper right corner. This has no immediate use, but I think it could prove useful in the future.
- Changed stepper motor terminal block type. The version 1.5 one can be difficult to get and has caused delays.
- Added a pull down resistor on the I2S clock signal. This mitigates startup pulses on some I2SO pins.

### V1.5

-  Change 5V power supply from MSP MP1584EN to Diodes Inc AP64350SP-13 
  - MP1584 is now obsolete
  - AP64350SP-13 increases the operating voltage from 28V to 40V
- Update Silkscreen
  - Removed references to functions on module pins
  - Added reference where Stallguard pins are hardwired to module pins.
  - Move JTAG closed to ESP32
  - Removed any axis letter reference and changed them to 1-6 to avoid confusion

### Future Changes

- Remove JTAG and make a module for it.
- Change LED to Lite On LTST-C170KGKT (too bright and make consistent with modules)

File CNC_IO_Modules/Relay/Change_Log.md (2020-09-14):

## Relay Module PCB Change Log

### V2.0

-  Changed transistor type

### Future Changes

- None Planned

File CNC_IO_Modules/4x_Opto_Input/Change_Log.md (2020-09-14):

## 4x Opto Input Module PCB Change Log

### V1.2

-  Change footprint of R9 to 0603.

### Future Changes

- None Planned

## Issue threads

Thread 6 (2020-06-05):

Ideas for next revision

MitchBradley, 2020-06-05:
* Schmitt trigger on limit and probe inputs for better noise immunity.  For example 74AHC14 (6 channels - need 2 of them, 12 cents ea from LCSC) or NL27WZ17 (dual, need 4; LCSC has them for < 6 cents).  Either way it is about 25 cents.
* And/or optocouplers on the inputs to make the board "bulletproof" (<- idea for board name).
* Add 4 pads at 0.1" or 2.5mm pitch in parallel with the terminal block, so either a JST XH 2.5 connector or dupont pins could be optionally stuffed, thus permitting easy plug-in of the connectors that are commonly found on NEMA 17 motors. If you don't want to make the board larger, the pads could be on the bottom for SMT connectors.  Smaller is not always better when you are trying to connect a bunch of cables...
* Bulk decoupling cap near ESP32 5V input.
* Layout all pin header connectors on a global 0.1" grid so that shields that span connectors can be made from protoboard.  For example a DB25 interface shield that picks up step/dir/ena from multiple pololu sockets and also inputs from the input module socket.
* Add series resistors, say 50R, to the shift register outputs, to reduce edge rates when the outputs go directly (via pololu socket bridge adapters) to external lines.  Could put the resistors on the adapters but then they are not just wires.

bdring, 2020-06-05:
Thanks

2 sided SMT would be very expensive for just one set of parts. I could put the pattern in front of the terminal blocks (unsoldered). If you installed the connector you could still use the terminal block in the vertical mode only.

MitchBradley, 2020-06-05:
Either way.  For the bottom mounted SMT thing, I was thinking that it would not be stuffed, just the pads so a user could hand solder if they wanted.

MitchBradley, 2020-06-05:
On my printer board the 0.1 pads are between the stepper module and the terminal block, but that arrangement needs a little extra space.  I am less impressed with tightly packed boards than I used to be, having recently refurbished two 3D printers with RAMPSy boards.  Fumbling with all the closely spaced connectors gets tedious.  Making the control board as small as possible just doesn't seem all that valuable for a DIY machine that is not likely to be optimized for space in every possible dimension.

bdring, 2020-06-05:
Do you have a SMT part number in mind. I would like to look at the FP.

MitchBradley, 2020-06-05:
The JST part is S4B-XH-SM4-TB   The DigiKey PN is 455-2262-1-ND

MitchBradley, 2020-06-07:
Optocoupled inputs?  PC817 optos are 5 cents.

bdring, 2020-06-11:
@MitchBradley  This is a circuit I used on another controller. Do you think there is a way to eliminate the diag jumpers? Maybe use an in-line resistor to protect any fighting outputs.

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

KingMo5h, 2020-06-11:
For what do you use these jumpers, do you even need them? If i understand Diag right, it pulls the 3V3 to ground too. I mean the only problem could happen when you have an external sensor. Then both of them can give u a stop or an error but isnt that even better? Is there a possibilty to deactivate Stallguard by software?
Btw. why u dont use EL847 or similar with 4 inputs and outputs.
And can you tell me when the i2c stuff is ready? I designed a pcb, but iam gonna wait till the software is done.

KingMo5h, 2020-06-11:
Also i would recomment you a big capacitor in the 5v rail in front of the esp32, since the esp32 sucks at wifi up to 200ma and can even reach 400ma for a short time and that causes the esp32 to fail/reboot. Iam not sure if this ever happend for your boards. Got it from this page (german):https://arduino-hannover.de/2018/07/25/die-tuecken-der-esp32-stromversorgung/

MitchBradley, 2020-06-11:
1. @KingMo5h is correct that it is possible to connect the DIAG0 or DIAG1 output from a TMC2130 or TMC5160 directly across the optocoupler output, since DIAG0/1 defaults to open-drain operation, active low on error.  TMC2209 cannot be used this way, since its DIAG is totem-pole, active high.  References:
[TMC2130 Datasheet](https://www.trinamic.com/fileadmin/assets/Products/ICs_Documents/TMC2130_datasheet_Rev1.12.pdf) Section 16 Page 72
[TMC5160 Datasheet](https://www.trinamic.com/fileadmin/assets/Products/ICs_Documents/TMC5160A_Datasheet_Rev1.14.pdf)  Section 16 Page 97
[TMC2209 Datasheet](https://www.trinamic.com/fileadmin/assets/Products/ICs_Documents/TMC2209_Datasheet_V105.pdf) Section 15.4 Page 66
To use TMC2209 without jumpers, it would be necessary to interpose an open collector buffer, or the equivalent made from transistors, between the DIAG output and the optocoupler transistor outputs.
2. 4-channel optoisolators would certainly work.  When I checked pricing at various distributors, one-channel optos were more cost-effective - about half the per-channel price of x4 optos. It is a tradeoff between cost and board real estate and board layout and assembly cost.
3. A bulk decoupling cap near the ESP32 5V input would indeed be a good idea.  I don't know if @bdring has experienced any of the boot failures cited, but it's good engineering practice to have one.
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
MitchBradley, 2020-06-29:
I2S input is definitely a possibility, and we chose the I2SO naming convention to allow I2SI as an option.  74xx597 is an alternative to '165.  The advantage of '597 is that the inputs are edge-triggered, whereas '165 are latched.  Edge triggered is more compatible with the I2S framing scheme.  On the other hand, there is at least one '165 (Nexperia 74LV165) with Schmitt Trigger inputs.  It is a little more difficult to support interrupt-on-change with I2S inputs compared to I2C, but do-able.

Bleeptech, 2020-06-29:
That was another possibility I was exploring was re-using the I2S0_WS and I2S0_BCK.. But I thought it might turn into a
major headache in the code to synchronise signals between I2S0 and I2S1 reliably..

MitchBradley, 2020-06-29:
I have not looked at this aspect of the ESP32 I2S interface in enough detail to know for sure.  On another SoC where I did extensive work with an I2S audio codec, there was an option to use a common clock for input and output.  I'm just guessing that is a common enough use case that the ESP32 might support it.

That said, I plan to make a very flexible input module around an STM32 microprocessor.  They are inexpensive and can do a lot of really useful thinks, for example offloading functions like display, encoder handling, and a menu system, in addition to bare I/O.

Bleeptech, 2020-06-30:
I had considered offloading the inputs to another micro-controller but I don't like the idea of introducing another MCU that
can hang, crash or just feed garbage data to a system controlling a laser, spinning cutter or other source of sudden pain..

 [INSERT GORY IMAGE HERE]

Non-critical things like displays, bells, whistles, etc no problem but anything where an MCU has to communicate with another
MCU in a critical system introduces another point of possible failure..

With TTL ICs a BCK of 320kHz [40MHz max via the I2S ports] can easily be used which will result in a sampling rate of 1kHz
per input and then it feeds to the same MCU controlling the driver outputs..

The x4xx165s were chosen for the load latches as the data on the inputs 'now' is what I want as I think that even with my
lack of code-fu I can keep the overall latency to <0.01 seconds..

Bleeptech's corollary to Newton's Second Law: Mass * Velocity = "OUCH! That freaking hurt!"

MitchBradley, 2020-06-30:
If the clocks are the same as for output, the bit rate is 8 MHz and the frame rate (sample rate) is 250 kHz.  Then you can choose how often you want to interrupt the processor to look at the data.

I don't understand what you mean about the latches.  The '597s also have input flip flops separate from the shifting stage.  The difference is in the details of the control signal sequencing.

I think the latency can be in the 100 us range, with the proviso that there will be CPU load to continually poll it.

There is probably nothing I can say about the other MCU argument; it is hard to counter a FUD (fear, uncertainty, doubt) position.

MitchBradley, 2020-06-30:
Let's consider a concrete example of a 14-bit I/O expander using a STM32F030 ($1) which has 15 GPIOs.  Use one GPIOs as TxD connected to an ESP32 UART RxD, at a baud rate of 1 MHz.  The code on the STM32 is essentially
```
uint16_t port_data = 0;
while (1) {
   unit16_t new_port_data = IN(PORTA);
   if (new_port_data != port_data) {
      port_data = new_port_data();
      UART_OUT(port_data & 0x7f);
      UART_OUT((port_data >> 7) & 0x7f | 0x80);
   }
}
```
The ESP32 code interrupts when a character is available and updates the port mask.  That only happens when the value changes, so the interrupts are infrequent, timely, and very easy to handle.  The latency is on the order of 20 bit times at 1 MHz, so 20 uS.

Making something like that reliable is far easier than what we went through to make the I2S output work correctly.  In the I2SO case the effort was worthwhile because the scheme's attributes are a perfect match for stepping.  That's not the case for input.

I chose 14 bits because that fits easily on an inexpensive micro.  Extending to many more bits is trivial, but would require a part with more pins, and the I/O module format would soon run out of connector space.  The latency could be reduced  by running the UART faster; it would probably go at least 2 Mhz and maybe 4, but it seems hardly worth it.

Closed 2020-07-12.

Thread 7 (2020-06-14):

Modules to test.

bdring, 2020-06-14:
I got a bunch of spindle modules to test.

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

The relay one is tested and installed.

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

Testing soon. RS485 modbus, 0-10V and 5V PWM.

Bleeptech, 2020-06-26:
Nice! I've been looking for a controller for an XXYZZ build with DM542A external drivers and this looks very promising..
A set of jumpers across the driver sockets should be enough to expose the signals I need..
Is there a machine file for this or have I not dug deeply enough into the code?

Bleeptech

P.S. Any chance you'd sell me a partially populated board and a set of the screw connectors?
[ I could breadboard it but they always end up looking like an LA freeway map.. LOL ]

bdring, 2020-06-27:
The latest version is on order. If it checks out I will be selling fully assembled versions.

There is a PCB version of the jumper you are talking about. The jumper just allows you to choose between a common ground or common 5V.

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

bdring, 2020-09-22:
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

bdring, 2020-09-22:
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

Closed 2020-07-12.

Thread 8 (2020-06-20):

MPG Jog Pendant Module Proposal

MitchBradley, 2020-06-20:
An input module that could connect to something like this:

[MPG Pendant](https://www.wish.com/product/5b10e987c25869171fbeb794)

Requires lots of inputs, so probably needs an I2C expander or something like.

KingMo5h, 2020-06-21:
That would be a great if this or similar could be integrated, I wanted to ask this too.
Yes probably needs a expander but the software work will be more challenging i guess.

Bleeptech, 2020-06-26:
It looks like the easiest solution might be adding a CH55x chip to handle the USB host functions..

bitluni stuffed one in his ESP32 powered micro game console..

https://www.youtube.com/watch?v=po3FBdY0GS4

MitchBradley, 2020-06-27:
It's good to know that is an option - but anyone who has ever dealt with programming USB devices might take issue with the word "easiest".

Bleeptech, 2020-06-27:
Been there.. Done that.. [Good thing I was already nuts before I started..]

ESP32 KE32-WROVER + GY521 with USB HID over Blueooth.. Enumerates as a joystick..

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

[Dont ask me to open the can.. Suffice it to say that it looks like R2D2 did a Jackson Pollock..]

yngndrw, 2020-07-17:
The [Contour ShuttleXpress](https://contour-design.co.uk/products/multimedia-controller/shuttlexpress/) might be a good option with a USB Host module.

LinuxCNC has a implementation which would save any reverse engineering:
https://github.com/LinuxCNC/linuxcnc/blob/master/src/hal/user_comps/shuttle.c#L64-L86

jschoch, 2020-07-27:
fixing the jog cancel race condition would be needed first.  I believe a much more complete jogging implementation was planned but it couldn't be fit into OG grbl.  Maybe the underlying jogging implementation should be fixed first?

MitchBradley, 2020-07-27:
Please include references to that race condition.

jschoch, 2020-07-28:
there are quite a few threads on the topic, here are a few.

https://github.com/gnea/grbl/issues/95

https://github.com/gnea/grbl/issues/837

https://github.com/gnea/grbl/issues/734

here is an attempted fix:  grblHAL seems to have this fixed and added a few features to support MPG

https://github.com/terjeio/grbl-Mega

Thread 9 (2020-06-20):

LCD Display/Control Module Proposal

MitchBradley, 2020-06-20:
A module to interface to an LCD display, for example:

[Ender LCD Display](https://www.ebay.com/i/254599064474)

It needs 3 input pins for the rotary encoder and its associated pushbutton, 2 output-only pins for the display, and one bidirectional pin for the display.  Optionally, there can be another output pin for the beeper, and another input pin for a pushbutton switch that is conventionally used for system reset.

Lots of software work would be necessary to use something like this.

There are similar displays (see [Reprap Discount Smart Controller](https://www.ebay.com/i/252815565682)) that need more pins - dual IDC cables instead of the one - because they run the display controller in 4-bit-data mode, and they also have an SD card slot.  The external SD card slot does have a mounting advantage, in that the slot can be located in a more convenient location.  That advantage is mitigated be the WebUI ability to upload files to SD from a remote computer.

There are also [touchscreen displays that have an onboard STM chip](https://www.ebay.com/i/223769115207) , that potentially could be used without much software work on the ESP end.  The on-board micro does all the menu stuff, and sends commands back to the gcode controller over an extra serial port.  Unfortunately they send Marlin commands, so it might be necessary to hack their firmware.

KingMo5h, 2020-06-21:
Maybe integrate the lcd of the tft35 or similar into the MPG Jog Pentant Module.
So everything works with the STM chip on the TFT and it sends only commands to the esp32 like you said but i dont know if the TFT has enough i/o pins or some expander could be included to get everything to work.

Aggebitter, 2020-11-09:
@MitchBradley
> There are also [touchscreen displays that have an onboard STM chip](https://www.ebay.com/i/223769115207) , that potentially could be used without much software work on the ESP end. The on-board micro does all the menu stuff, and sends commands back to the gcode controller over an extra serial port. Unfortunately they send Marlin commands, so it might be necessary to hack their firmware.

Firmware for GRBL: [https://github.com/makerbase-mks/MKS-TFT/tree/master/MKS_TFT_CNC]

MitchBradley, 2020-11-09:
Yeah, I have one of those on one of my 3D printers.  The stock firmware is mildly configurable, but mostly in the way that screens are presented.  There is an open source version of the firmware, so hacking would be possible, if perhaps tedious.

Someone recently informed us of this, which looks much more suitable:  https://github.com/mstrens/grbl_controller_esp32 .  It could be wired to a second serial port on some Grbl_Esp32 pins, especially if one has Bart's new 6-pack board with plenty of spare GPIO pins and plug-in IO modules. It uses a second ESP32, so it ought to be possible to connect it wirelessly by hacking its firmware to talk over bluetooth, which would then work with any Grbl_Esp32 board with no hardware mods.

Skywalkerf34, 2021-12-28:
This is available now on TINDIE here :
 https://www.tindie.com/products/24799/
https://www.tindie.com/products/24731/

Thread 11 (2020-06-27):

Version 1.0 Uploaded

bdring, 2020-06-27:
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

A new version has been designed, added to [the repo](https://github.com/bdring/6-Pack_CNC_Controller/tree/master/versions/V1p0) and 10 samples ordered.

- Fixed issue where StepStick and SD card conflicted.
- Switched from (2) spindle modules to (5) universal CNC I/O Modules.

The CNC I/O Modules idea is [defined here](https://github.com/bdring/6-Pack_CNC_Controller/wiki/CNC-Module-Definition). More details will follow. 5 different test modules were ordered.

KingMo5h, 2020-06-27:
Looks nice.
Btw the traces in the left corner (StepStick socket) is different then the others. It has 90° instead of 45° like the others.

bdring, 2020-06-27:
Thanks for the tip on AP64350SP-13

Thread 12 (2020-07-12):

Version 1.1 Uploaded

bdring, 2020-07-12:
Testing of version 1.0 went great. There were no real issues with the hardware. I made a few small tweaks and released 1.1 for a small production batch.

- Tented the vias. That was a setting that accidentally got flipped in my software.
- Moved a couple vias away from pads.
- Added a 5V power LED
- A lot of silkscreen improvements.
- Moved the JTAG under CNC Module #1

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

Dan018, 2020-07-14:
This board will do everything I am looking for ! Great work!

I would like to get some of these boards made. Is the v1p0 uploaded here OK to produce, or should I wait and produce version 1.1 (v1p1?) when the diptrace is uploaded?

bdring, 2020-07-14:
I am sorry, I forgot to push the changes. V1p1 is available now.

I have 20 fully assembled pieces on order from PCBWay as a production test. They take about 4 weeks. I also have all the modules on order too.

If you want to assemble yourself, you could probably do it faster.

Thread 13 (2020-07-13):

Tool changes...

atlaste, 2020-07-13:
One thing I've been thinking about a lot is the issues I'm having with tool changes and top probing. You usually want to have 2 things exact: (1) the tool position and (2) the piece.

I've basically came up with this idea:
For (1) you can use a simple probe fixed at the homing spot. When you go down, the probe will hit and because it's fixed, you know the z coordinate.
For (2) you can use something like a servo with a switch. Actually some people have reported very good z-indexing with this approach, it's quite easy to DIY, quite resilient to dust and easy to place next to a spindle.

With these two things, it should be possible to do a proper mill & any tool change. First, you home and move down until you hit the probe, that's Z1. Before milling, you basically put the spindle above the piece, the CNC can move a bit to where the servo is, go down until its hit and you know Z2. Next, start milling till the first tool change. No need to move manually down anymore, because we already know where the piece is.

Tool changes can now be done quite easily by a delay, by storing the X/Y coords, changing the tool, homing, probing (Z3), moving back up and moving back to X/Y. With the difference between Z2 and Z3, the software can compensate for the difference and do the rest.

What does this has to do with the controller? Obviously, a lot has to happen in software, but the hardware needs to support a 'servo with a probe switch on a stick', as well as a second probe. Not sure how hard that's going to be...

bdring, 2020-07-15:
Grbl_ESP32 supports custom tool changes. If the user supplies functions to handle the custom motion, it will run those functions when the Gcode includes tool change information.

The Atari plotter machine definition is an example of how this works. It has 4 pens in a changer. When it sees the M6 Txx gcode it runs a special sequence to change the pens.

https://www.youtube.com/watch?v=XTdoDOojJFQ

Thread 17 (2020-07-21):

Obsolete Power Supply IC

bdring, 2020-07-21:
The MP1584EN power supply IC obsolete. I have been using it for years and did not notice it until recently. My PCB supplier has no trouble getting them though.

I have a test controller on order with the [Diodes Inc AP64350SP-13](https://www.diodes.com/part/view/AP64350). It is very close in capability and has a higher max input voltage. I will switch to that if it works out.

KingMo5h, 2020-07-22:
Thats the one iam using. Works fine without problems.

abrackers, 2023-01-08:
For the external driver version, the TPS54360 (C44377) is specified, however it seems to have been replaced by the TPS54360B version (C524806). Is this just a drop in replacement or will I need to change some other components?

bdring, 2023-01-09:
Let me Google that for you

I found this.

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

Looks like it is just a polymer coating. It should be a drop in replacement.

Please consider donating to the project.
http://wiki.fluidnc.com/#donations

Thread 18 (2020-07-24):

External Driver Connector Module Source Files - References #5

wocpsu, 2020-07-24:
Could you please post the source files for the external stepper motor driver jumper board?
This references issue #5

bdring, 2020-07-25:
[Added](https://github.com/bdring/6-Pack_CNC_Controller/tree/master/External_Driver_Adapter)

Closed 2020-07-25.

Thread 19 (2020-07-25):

Optimize Pin Header Orientation of CNC Modules for Active Cooling

MCTaylor17, 2020-07-25:
This is more of a question than a suggestion because I'm not that familiar with electronics or the vision for the CNC modules.  It also might be a low priority, version 2 or 3 consideration because I suspect it involves a lot of rework.  With that said, let me explain what I'm doing and my observation about the current orientation.

I'm taking a small stab at designing a 3D printed fan enclosure which got me thinking about the thermals.  My high level plan is a top-mounted fan blowing down over the board with dedicated ducting to channel air more directly towards the stepper drivers.  With respect to the CNC modules, I'm thinking I can provide similar ducting for bays 2, 3, and 5 while reserving bays 1 and 4 for lower current applications like sensors.  Based on the universal/prototyping nature of the board, I'm thinking it might be useful to add some butterfly valves to provide selective granularity over which drivers/modules receive the most cooling.

Now, I notice the alignment of the pin headers currently forms a wall from the center, effectively blocking the underside of the boards.  I'm wondering if it would be beneficial to reorient the headers 90 degrees (see below, green proposed, red existing) to allow for air flow beneath the boards.  This would provide both the option to allow air flow for active cooling, or to block it off to increase airflow elsewhere.
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

This primarily comes down to one question: How likely do you think it is that the underside of the boards will require cooling?  For example, the TMC2208's recommend this type of cooling (see below).  I'm not sure how much of that is a function of space constraints, but "low-profile" CNC modules could be desirable for some applications.

If you don't envision the underside ever needing cooling, the current orientation is actually quite smart, in which case bravo!!

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

bdring, 2020-07-26:
Hey Mike,

Thanks a lot for the input, but it is a little too late to make any changes. The motherboard was prototyped twice, a couple of the modules were prototyped more than once and there is a lot of production hardware no order. I can give a little insight into my thought process on the layout.

### Size

I wanted to appeal to small scale DIY CNC machine designers. I did not want a completed controller to end up being so large it would not be consider for small scale machines. I mocked up a basic set of modules and tried to see  how much width I needed for the external interfaces. The widest was the 4x input module. It has 4 terminal blocks with 3 terminals each.  There also needs to be a mounting screw along that edge. Placing the microcontroller interface on any edge except for the opposite side would have made the modules even wider.

One last thing I considered was a mini, budget, 3 axis version that is about 1/4 the size. This relies on the modules hanging off the motherboard. I have not finished the design, but here is a sneak peek.

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

### Isolation

A lot of DIY CNC machines suffer from electrical noise and spikes. This can be difficult to fix and can be a mess of last minute fixes. This is especially true on the inputs. I wanted to design some "bulletproof" modules that you can expect to plug in and just work. Also, when you use relays that are connected to high current DC or AC, you want to isolate that. Putting the external interface as far away from the microcontroller interface seemed like the logical way to solve this.

### Cooling

I did not consider underside cooling. The board currently does not support UART type drivers like the TMC2208. I am not sure why you would choose that driver unless you already had some. You will get better performance out of the TMC2130 and TMC5160 drivers. I assumed top side cooling would be sufficient and I placed 2 fan connectors, one on each end of the board near the drivers. I think if you really want to push some power, you should consider external drivers.

None of the current crop of CNC modules need cooling. If high current modules for motors are used, they should integrate their own cooling. The module socket connector is not designed to provide a lot of current anyway. The spec says that should also come from off board.

I would love to see what you come up with for an enclosure.

MCTaylor17, 2020-07-26:
Thanks for the response. I'm really loving your design philosophy. Sounds very reasonable to me.  Especially the point about isolation considering most of the terminal would sit between it's own and a neighboring header.  Considering you want 3rd party module development, isolating the headers like you have is really smart.  Will save a collective ton of troubleshooting hours over the years 🙇‍♂️

My only question from the above is regarding module cooling.  I was considering ducting for the modules because your video suggested there may be future support for additional drivers.  I'm kinda hearing those will require their own power supply and cooling fan.

For myself, I don't have any plans for high power steppers just yet and part of designing an effective cooling case is to delay that need as long as possible.  I think what I'll do is forget the modules and design strictly for cooling the steppers (and the ESP32 if you think it needs it?), just to keep things simple.  No need to future proof and over engineer a simple enclosure.  After all, I only need 4 or 5 steppers for what I have in mind.  Once I hit 6 I'll start worrying 😂

Closed 2020-07-26.

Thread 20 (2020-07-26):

10-30 V inductive endstops

raenji-sk, 2020-07-26:
Would it be possible to upgrade the end stop module to support 10-30V inductive sensors (ideally both PNP and NPN)?

bdring, 2020-07-26:
You could build it with a different isolated power supply and led resistors to use 12v NPN sensors.

yngndrw, 2020-07-26:
The [switch input module](https://github.com/bdring/6-Pack_CNC_Controller/wiki/4x-Switch-Input-module) just requires the signal pin to be pulled to ground, so it should already work with open collector / NPN outputs. The power supply for the sensors would need to be handled separately.

PNP sensors would require a little more work, essentially you have to [convert them to an NPN output with an external NPN transistor](https://electronics.stackexchange.com/a/255677):
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

KingMo5h, 2020-07-26:
The cheapest isolated DC-DC converter and with 2W I could find are the Meanwell SPUN02L, either 5V, 12V or 15V Output. Input is 5v 12v or 24v. Maybe it helps.

raenji-sk, 2020-07-27:
OK, thanks. I will look into it when I have some time. I've been using GRBL for a long time and am looking for some other hardware as well as the 8 bit is clearly limited these days. This board seems very nice and I would not have to get used to a new controller / software and keep on using GRBL with better hardware.

raenji-sk, 2021-10-08:
@M10CUBE Sorry that was the first and last version. I had the board made in China but never assembled it (I never liked the integrated drivers much to be honest). Went for grblhal and teensy 4.1 board instead. That worked quite well for me for a year or so. But that's history now too as I changed the cnc controller to Uccnc.

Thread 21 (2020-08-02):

RC Servo/BESC CNC I/O Module

bdring, 2020-08-02:
Here is a simple CNC I/O Module to add a couple of RC servos or a BESC (Brushless Electronic Speed Controller).

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

It has a switch to allow the servos to be powered from the controller's 5V (limited current) or an external power source. Some bigger servos like a higher voltage, so that could be provided through the terminal block. Grbl_ESP32 also supports BESC based  spindles, so you could use this module for that as well.

There are other ways to get more servos via I2C PWM controllers, but this is a just a simple one that requires no changes to the firmware.

bdring, 2020-08-10:
Here it is.

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

plangenh, 2020-10-10:
Thanks a lot for this great modular project!
Are you planning to upload the Source files of this RC Servo Module in the CNC_IO_Modules directory as well?
I am planning on using two servos and would be really interested in the files. I'd order the module on tindie, but shipping to Germany is really expensive.

bdring, 2020-10-10:
I uploaded the source files and gerbers. I am sorry about the shipping cost, but I am only shipping via Priority Mail during the pandemic. The other methods are taking up to 3 months.

Please consider a donation to the Grbl_ESP32 project.

plangenh, 2020-10-11:
Thanks a lot, really appreciated!!
Will definitely donate to the project.

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

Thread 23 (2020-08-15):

Just for fun....3 Pack

bdring, 2020-08-15:
I needed to test a new DC-DC power supply, so I decided to make a mini controller at the same time.

This is tiny controller that uses CNC I/O Modules. It is about the size of an Arduino Uno. It has sockets for 3 axes and 3 modules. Other than the power supply, there is no active circuitry on the board. It took only about an hour to design. It shows how the modular concept allows you to quickly prototype a controller with professional level accessory support.

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

Skywalkerf34, 2020-08-15:
Nice design, as already said modular design helps a lot, then "just" route a new board and that's it !

bdring, 2020-08-17:
It would be interesting to make a 5V DC-DC module.

It would use the VMot to output 5V using the module pins. That would further reduce the  complexity of the base controller.

Closed 2020-09-11.

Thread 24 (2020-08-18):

Getting ready to sell a few

bdring, 2020-08-18:
I am just about ready to sell some controllers. I did a small test production that went perfectly. I have about 15 to sell before I order more. I have all of the modules except the 5V Output (PWM, Lasers Etc). That is due soon. There was a delay on one of the parts.

I want to sell to people who have built a machine successfully before and have some experience with Grbl_ESP32. The goal is to get them into use as fast as possible. The hardware is pretty solid, but the firmware might be tweaked a bit. Expect to have to load the firmware a few times.

If you are interested reply to this post. It would help if you give some details about how you plan to use it and the modules you would need.

The price will be released soon, but expect the main controller to coast in the $40 - $50 range and the modules are $10-$20 range depending on the complexity.

tgirard, 2020-08-19:
I'll buy one. I bought one of your first grbl controllers and loved it. I'm using 2209's with sensorless homing on my MPCNC. I would like to get two relay modules and an input module if you have them.

Let me know
-Timothy Girard

bdring, 2020-08-19:
Here is the price and availability right now.

$45 for the 6 Pack Motherboard

$20 for the 4x Input Module
$20 for the RS485 Module
$18 for the 0-10V Spindle Module (no stock yet, on order, delivery TBD)
$12 for the Relay Module
$11 for the 5V Output module (no stock yet, on order, delivery soon)
$10 for the RC Servo / BESC module
$4  for external driver adapters.

$25 for a pre-programmed Grbl_ESP32 to your requirements.

They would be sold via PayPal for a while....then Tindie

contact me via bdring  <at> buildlog.net

tgirard, 2020-08-20:
Thanks Bart,

Buildlog.net is not co-operating

Can you please just send me a link where I can put the order in and paypal you?

Thanks

-Tim

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

bdring, 2020-08-20:
Contact me via DM on Slack. [Here is an invite link](https://join.slack.com/t/buildlog/shared_invite/zt-7twbithi-bRGScOaCgJoBpTbkykfxoA)

xP373Rx, 2020-08-29:
I was looking for a board like that for a while.. Im running grbl on my cnc with esp32 and i love the simplicity of uploading and working with it. I also own 2  3d printers. Which i would like to use esp32 on. I got marlin compiled for esp32  and its running but esp simply has to few IOs if you have more then 3 axes and extra sensors. You could basically make some mosfet and thermistor modules and make a great wifi printer board out of that. Current solutions work with serial wifi modules which are rly slow on upload. It would be a true board for all cnc and printer nerds ;> As for display , you can use serial and existing marlin compatible displays. Marlin already supports lucs webinterface. the only thing that needs to be added is support for your modules.

Great work on the GRBL port >;

Closed 2020-09-11.

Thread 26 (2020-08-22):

New CNC I/O Module - Dynamixel Servos

bdring, 2020-08-22:
This allows you to control Dynamixel servos. Dynamixel servos are on a bus, so you can connect a lot of them. I put two connectors, because you might have servos on either side of the controller. If your controller VMot is in the Dynamixel power range, you can use that. There is also an external connection to supply that voltage.

Here is a [video of a delta running these servos and Grbl_ESP32](https://www.youtube.com/watch?v=wPDP6ckP0sQ)

I also added a single RC Servo connector, because I had an extra I/O pin.

I'll probably wait to order this until I can join it with another order to save on shipping.

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

bdring, 2020-09-08:
Here is the module.

- It can pull servo power from VMot or use an external voltage (the switch).
- It has (2) Dynamixel Servo connectors. The servos are on a bus, so you really only need one, but this helps if servos are on either side of the controller.
- One normal RC Servo connector.

Still testing right now.

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

bdring, 2020-09-10:
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

Skywalkerf34, 2020-09-29:
Hi,
Can we use ESP32 GRBL to drive DELTA with this kind of smart servo?
which parameter ?
any machine def example?

bdring, 2020-09-29:
There is a partially working example that will be complete within a week or two.  Please be patient.

Here it is running an older version of Grbl_ESP32.

https://www.youtube.com/watch?v=wPDP6ckP0sQ

I cannot provide any free support for using the delta. It is not part of the core Grbl_ESP32 project.

Skywalkerf34, 2020-09-29:
Will wait for this example, thanks

Closed 2020-09-11.

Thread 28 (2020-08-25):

wiki updates socket pins and external module soldering tip

jschoch, 2020-08-25:
for the external stepper module  it is easier to solder the inner voltage selection pins first, may be a helpful note to add to those instructions.

for the Socket Pin Number Mapping if the default pins are unlikely to change it would be helpful to add them to the list and for them to match the order on the board.  for example:

```

// #4 GPIO_NUM_34 (input only) default: A_LIMIT_PIN
// #3 GPIO_NUM_35 (input only) default: Z_LIMIT_PIN
// #2 GPIO_NUM_32  default: Y_LIMIT_PIN
// #1 GPIO_NUM_33  default: X_LIMIT_PIN

```

also the i2s_out_xyzabc.h is different, it isn't clear why but it would be nice if it matched or if it was clear what the difference was intended for.

```

// Socket #1
// #1 GPIO_NUM_33  default: C_LIMIT_PIN
// #2 GPIO_NUM_32  default: B_LIMIT_PIN
// #3 GPIO_NUM_35 (input only) default: A_LIMIT_PIN
// #4 GPIO_NUM_34 (input only) default: Z_LIMIT_PIN

```

bdring, 2020-08-25:
I don't follow you on the socket mapping suggestion.

FYI: On the next version of the 6 Pack (on order), the silkscreen changes to remove any axis references. It is very likely that people will not use the sockets for XYZABC.

The only hardwired issue is the stallguard wiring, so there is a reference to that. If you are using the stallguard for motor number #1, you cannot use the socket #1 pin attached to it.

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

jschoch, 2020-08-26:
`I don't follow you on the socket mapping suggestion.`

with the 4 input board you can't see any of the silk screen so you have to take it out to figure out what is connected.  The order of the pins in the wiki also doesn't match the physical order of pins.  You could name the "signal" pins like this:
Sig<Module #>:<1..4>, e.g Sig5:2 which would map to ISO(27)

regarding i2s_out_xyzabc.h vs i2s_out_xyzabc_trinamic.h I now see that there are also 6-pack specific machine files in the Machines dir, and I had made the bad assumption that i2s_out_xyzabc_trinamic.h was for the 6-pack board.  For someone using external steppers it may not be clear which file to use.

bdring, 2020-08-26:
The numbers are correct as far as I can tell.  Are you orienting signal #1 correctly. With your format Sig5:2 would be ISO(25) not 27.

I can add these two images for reference.

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

bdring, 2020-08-26:
The I2S_out... machine def predates the 6 Pack. It was used for I2S when it was still a bread board.

Most people are looking for 6 Pack in the name. I can kill it off soon.

jschoch, 2020-08-26:
sry, i don't know which diagram I got ISO(27) from.  Sig5:2 would be ISO(25) would be a good way to disambiguate the mappings.

I also noticed there are no control pins mapped by default, maybe no one uses them.  It would be nice if you had them mapped out as defaults and or commented out defaults in a way that had shows what would need to be swapped.  For example

```
/*

// To enable control pins you must disable another function such as MIST
// Instructions for setting up external pullups: <link>
// Instructions for the opto input module control pin configuration<link>

 #define CONTROL_RESET_PIN       GPIO_NUM_2  // default pin: Sig2:1   Swap for MIST default pin
 #define CONTROL_FEED_HOLD_PIN   GPIO_NUM_36  // default pin: Sig2:4 needs external pullup without input module
 #define CONTROL_CYCLE_START_PIN GPIO_NUM_39  //  default pin: Sig2:3 needs external pullup without input module

/*
```

bdring, 2020-08-26:
There are no defaults. I can add it as an example on the 4x Input page. Very few people use them. Macro buttons are trending though.

I have been getting a lot of practice writing them for people who order pre-programmed ESP32s.. Hopefully a useful style will emerge. I put them here.

https://github.com/bdring/6-Pack_CNC_Controller/tree/master/machine_defs

Closed 2020-09-11.

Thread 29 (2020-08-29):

Feature Suggestion: split VMOT into VMOT+VAUX

StephS, 2020-08-29:
Personally I'd like to be able to run my motors at 36v or 48v and I know there are TMC5160 drivers that support this, but the 6-Pack is limited by the onboard VR and a few other components.
What do you think about splitting VMOT into two rails, one rails specifically for the stepper drivers, another for the rest of board/aux power like fans, etc. This would allow the board to be powered by say, 12v which would allow the cheaper/easier to find fans, and the steppers could be up to 36v without any other changes to the board. It would also eliminate some noise on the AUX, as you could run separate power supplies (a single power supply can still power both).

bdring, 2020-08-29:
These are some good suggestions for even more reasons than you have mentioned. I'll consider it for future revisions. FWIW: The next batch will allow 40V input, due to upgrading the obsolete p/s chip.

At some point you do have to consider the limitations of current and power dissipation in the Pololu socket.

yngndrw, 2020-08-30:
> At some point you do have to consider the limitations of current and power dissipation in the Pololu socket.
For me, this is most important when using a mixture of onboard and external drivers. E.g. When using JMC servos for the maix axes.

In this case, it would be nice to use a single motor power supply.

Aggebitter, 2020-09-25:
I totally agree on spliting VMOT into VMOT + VAUX. I use ~4A external drivers driven @ 48V on LinuxCNC . Depending on MOSFET used in tmc5160 the six-pack is a replacement candidate on my modified EMCO F1 mill.

fladdie, 2021-12-27:
Is there any news here yet? I am currently looking for a new cnc controller board. I would very much like to run tmc5160 driver with 60V.

StephS, 2021-12-27:
I made a fork of the design here:
https://github.com/StephS/6-Pack_CNC_Controller/tree/Kicad-v1p8s/versions/V1p8s

It includes the split VMOT along with some layout changes.
I've already had 5 boards made, but I need to buy parts and assemble and test.
Gerbers are included, so feel free to download and send to your favorite fab. However I haven't rebuilt the BOM yet.

fladdie, 2021-12-28:
Hi Stephanie,That sounds great. I will order a few boards tonight.Is it possible to run the drivers at 60v with your modified board?In the PDF 6_axis_I2S_v1p8s.pdf vmot is labeled with 12-40v.Am 27.12.2021 22:03 schrieb Stephanie ***@***.***>:
I made a fork of the design here:
https://github.com/StephS/6-Pack_CNC_Controller/tree/Kicad-v1p8s/versions/V1p8s
It includes the split VMOT along with some layout changes.
I've already had 5 boards made, but I need to buy parts and assemble and test.
Gerbers are included, so feel free to download and send to your favorite fab. However I haven't rebuilt the BOM yet.

—Reply to this email directly, view it on GitHub, or unsubscribe.Triage notifications on the go with GitHub Mobile for iOS or Android.
You are receiving this because you commented.Message ID: ***@***.***>

StephS, 2021-12-28:
The limiting factor will be the capacitors for the stepper drivers, and the stepper drivers themselves.
That's one of the things I need to verify on the BOM.
The other would be all the footprints and make sure there aren't any manufacturing issues. Apparently the voltage regulator is hard to come by.

So just note that while the design passed DRC and ERC, it's still untested.

If you don't mind waiting a day, I'm thinking I can pull the parts off my old 6-Pack board.

StephS, 2021-12-28:
So I took a quick look, and the result is that the stock capacitors are 330uF @ 50v. This is why the 40v max rating. I looked for replacement capacitors that are rated >60v and couldn't find any in the same package size. The closest was 150uF @63v which is a significant drop in capacity.

You could do a through hole cap as there are 270uF @ 80v which would work quite well. However this would require either modifying the board, or bending the leads and making a fixture to hold them and prevent damage.

Modifying the board would be the best route, by adding holes for through hole capacitors. It could cause an issue with the SMT caps sharing the same pads, but maybe that can be worked around.

Skywalkerf34, 2021-12-28:
Think also that Two capacitor in// give sum of the capacitor, this is what we do for our board here because of form factor :  https://github.com/Skywalkerf34/6-Pack_CNC_Controller/tree/master
With this way we can keep the capacitor under the Pololu socket

fladdie, 2021-12-28:
First of all, thank you for your quick response.
I would like to use the TMC5160 pro drivers from Bigtreetech. https://www.biqu.equipment/de/products/tmc5160-pro-v1-0 because they can be used up to 60V (56V).
If I understand correctly the problem with Stephanie's board are the capacitors.

Skywalkerf43 suggests to put two of the 63V capacitors suggested by Stephanie in // to get back the capacity that would be necessary.

I also like the board from Skywalker. Especially the fact that I could buy it directly on Tindie. Unfortunately, it will not be so easy to convert the board to 60V, right?
28. Dezember 2021 12:58, "Francis" ***@***.*** ***@***.******@***.***>)> schrieb:
	Think also that Two capacitor in// give sum of the capacitor, this is what we do for our board here because of form factor : https://github.com/Skywalkerf34/6-Pack_CNC_Controller/tree/master (https://github.com/Skywalkerf34/6-Pack_CNC_Controller/tree/master)
With this way we can keep the capacitor under the Pololu socket

	—
Reply to this email directly, view it on GitHub (https://github.com/bdring/6-Pack_CNC_Controller/issues/29#issuecomment-1002056150), or unsubscribe (https://github.com/notifications/unsubscribe-auth/ABPVDDA5ICHXKLUQR7XZL5TUTGQ4LANCNFSM4QPCVSAA).
Triage notifications on the go with GitHub Mobile for iOS (https://apps.apple.com/app/apple-store/id1477376905?ct=notification-email&mt=8&pt=524675) or Android (https://play.google.com/store/apps/details?id=com.github.android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).
You are receiving this because you commented.Message ID: ***@***.***>

bdring, 2021-12-28:
I don't know the details of that controller, but often the 5V DC-DC power supply can not handle inputs as high as 60V.

I would be careful running those drivers close to 60V. Back EMF from the drivers can causes spikes a few percent above the VMot. I would suggest 10% derating.

StephS, 2021-12-28:
Completely agree. And I checked the biqu website, and while the driver states they support up to 60v, 56v is the recommended max. Looking at the TMC5160 datasheet, I have an idea why.
The VSA pin on the 5160 drives an 11.5v internal voltage regulator. On the datasheet section 3.2 it recommends not driving this more than 40v due to significant self-heating.
These stepstick style drivers aren't the best with heat dissipation either, so you'll likely need to derate your max current.

As for my fork of the board, the layout would need to be significantly changed to support two capacitors.

The fork by @Skywalkerf34 uses a voltage regulator with a max of 50v, so you'd be limited there.

If you really want 60v, the TMC5160 datasheet recommends 100uf of bulk capacitance per amp of drive current.
I can look into making room for a larger capacitor, but it definitely becomes a bit difficult with space and layout constraints.

Skywalkerf34, 2021-12-30:
If you power with 56 volts PSU, There might be a way to fork my design cutting some track, using external fuse  and use the footprint to modify power inlet , then change the 2 SMD capacitor for one 100 mF 63V wired in same place.
Of course this will be a  fork handMade for you....let me know if you can be interested in

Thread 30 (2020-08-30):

New CNC I/O Module - High Current FET

bdring, 2020-08-30:
I finished the design for a high current FET module.

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

This uses an external supply hooked up to the terminal block in the middle of the board. The removable terminal block can be mounted for vertical entry of the wires or horizontally from the right or left.

The FETs are On Semiconductor NCV8403A rated at 42V and 15A. The terminal blocks are rated to 6A per terminal. The FETs have integrated diodes to protect them on inductive loads. There are 4 independent channels with LEDs to show the status of each channel.

This would be ideal for driving solenoids and valves.

I will be ordering a batch within the next few days, along with the other 2 recent designs.

bdring, 2020-09-08:
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

Closed 2020-09-11.

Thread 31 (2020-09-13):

ESP32 do support 5V input on GPIO's

Aggebitter, 2020-09-13:
I have been using 5 volt devices on ESP32 for years no issue at all and already in 2016 it is confirmed by Espressif.
The ESP32 does actually have an internal snapback circuit that protects it from overvoltage.
The Wiki should address this part in sections that says the opposite.

From an old tread at Hackaday
https://hackaday.com/2016/07/28/ask-hackaday-is-the-esp8266-5v-tolerant/

The facebook group on ESP8266 where the confirmation is made by Espressif CEO Mr Teo Swee Ann
https://www.facebook.com/groups/1499045113679103/
search for Teo Swee Ann in the group

Teo Swee Ann
"i can reply officially here: it is 5V tolerant at the IO. while the supply voltage is at 3.3V."

Teo Swee Ann
"Baoshi Zhu **ESP32** and ESP8285 are both 5V tolerant as well."

Teo Swee Ann
"but for ESP32, it is a very complicated matter. it supports 1.8V operations too... i don't know where to start..."

Teo Swee Ann
 "the reason is too many users took it to mean that the chip is 5 V tolerant. When we say 5 V tolerant, we are only referring to the IOs. So some users mistook this to make that they can power the chip entirely off the 5 V supply. The correct usage is to use 5 V open for these 5 V tolerant pins, and only via **only drain configuration**."

Regards
"Onkel David now with a 6-pack"

bdring, 2020-09-16:
Thanks for the information. I did not know that.

Aggebitter, 2020-09-25:
Closing it
A remark when using mechanical limit switches. The signaling voltage is higher at 5V and when doing analog filtering the filter works a lot better as the SNR gets higher from the stepper driver noise. That is why I always used 5V signaling for my endstops.

Closed 2020-09-25.

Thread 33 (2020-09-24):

Possible 3D Printed Case Concept

bdring, 2020-09-24:
I prototyped a bit of a new case concept for the 6 Pack. I wanted to keep the flexible, modular concept. If you change out a module, you shouldn't need to redesign the case or even disassemble it.

This uses a base and a partial cover for the motherboard. There would then be individual covers for each module. The design is far from complete, but I printed a few pieces, to get the feel for it. There would be a mounting flange along the bottom and possibly some mounting features for the module covers.

Any thoughts or ideas are appreciated.

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

jaysettle, 2020-09-26:
This looks good, I would like to have the file if it's available.

bdring, 2020-09-26:
It is not finished yet. I will post them soon.

What are your thoughts on mounting holes. I thought a flange could be added to the sides. Another thought is to have mounting holes on the floor of the base. It could keep the size down and look cleaner.

What are your thoughts on module covers. I am OK with no covers.

jaysettle, 2020-09-27:
Mounts on the bottom and sides would be great this can be added. I will use them if they are there.
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

bdring, 2020-09-28:
I don't like the cover mounting. It make it difficult to remove when mounted. I made 2 versions. I can post them both.

Side mount

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

Internal mount

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

jaysettle, 2020-09-28:
My install might be a one off. I won't be able to use either of those I'm using an ammunition case as a controller home. I can modify the file on my own though no problem.

Bleeptech, 2020-09-28:
Looks like a nice bulletproof case build. ;D
I'm going for fireproof myself and recycling old fire alarm panel boxes for mine. LOL
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
They're about the same gauge of steel as the ammo cans and you can usually find them cheap or free in the recycle pile at
your local alarm installer.

bdring, 2020-09-29:
The files have been added to the Repo.

https://github.com/bdring/6-Pack_CNC_Controller/tree/main/3D_Files/case

Click on the files to use GitHub's 3D viewer.

truglodite, 2021-03-14:
Bart, the case looks decent, however for myself I would have to redesign it so it would not get aluminum chips inside. Instead of doing all that, I made a larger "dust hardened" box to house all of the electronics (6pack, pi3, 7" touchscreen, psu, relays, 80mm fan, 40mm fans per hot device, etc). It's a one off design made from mahogany (looks purdy for sure).

Ideally the 6pack enclosure (any cnc controller enclosure for that matter) should come in one of 2 types, 1) A tinker friendly coverless mount designed to plop into a larger dust hardened box, which has integrated fan cooling, or 2) A stand alone dust hardened enclosure for just the controller board. What you have right now doesn't fit type 2 requirements, and the standard feet type mount you have is a better fit for type 1. IMHO, an enclosure should be designed to meet type 2 requirements... dust filtering for the fan ports at least, and careful design that does well at shedding chips (ie, not place for alum chips to hide and drop inside when opening the enclosure).

I did some remixing/designing to make a "type 2" enclosure for my old ramps setup. It had a "pitched roof with gutters" on top, and a scotchbrite filter for the fan. So I have some ideas I've already brainstormed for the 6pack. Let me know if you want help on this.

Side note... I RE'd the stl model for the v5 board to design a 1pc open mount for my rig. In doing so, I noticed the hole spacing was a bit smaller than the board itself (~2mm short on the diagonal). Scaling my model to 104% fixed it. Not sure if that's an error on JLC's part, or maybe you nudged the holes out a bit and just forgot to update the stl.

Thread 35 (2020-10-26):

PCB manufacturing

simonemery555, 2020-10-26:
Hi Bart,
i live the UK so the postage from tindie is pretty expensive, so i thought i would get it made and have maybe with the minimum orders of 5 usually, id have spare for my other projects.
Please can you let me know where you had them made? did you assemble then your self? i searched on PCBWay but it was not there

thanks in advance!

Simon

bdring, 2020-10-26:
I buy from PCBWay. I did do any order sharing there.

I can ship for $18, but it could take a while. Probably about the same time as a PCB way order. 4-6 weeks.

simonemery555, 2020-10-26:
is the 3-6 days listed on their website not realistic?

bdring, 2020-10-26:
That is for raw boards. Assembled boards take at least 3-4 weeks. This
board has some terminal blocks that are not available in China, so that
adds some time. My last order was placed on 9/17 and arrived 10/24.

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

--
Bart Dring

"If you did not build it, you will never own it"

simonemery555, 2020-10-26:
ah crap. i've not ordered them before. thanks for the eye opener :)

do you have any ready made to ship?

bdring, 2020-10-26:
Yes, I have a lot of the main boards.

I am out of stock on the 4x input modules to interface switches. I am
tracking a delivery on those for Wednesday. If you order from Tindie on
Thursday I should have those.

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

--
Bart Dring

"If you did not build it, you will never own it"

simonemery555, 2020-10-26:
okay - do you have a link for the $18 shipment?

bdring, 2020-10-26:
I do not. It will ship USPS First Class Package. If you place an order, I will refund the difference from the higher priced shipping.

 I do not want to add that shipping option, because some countries would be way too slow during this pandemic.

simonemery555, 2020-10-26:
sure, understood. I'll stick the order in.

simonemery555, 2020-10-26:
6 Pack Universal CNC Controller - Include Programmed ESP32: Include Programmed ESP32
External Stepper Motor Driver Adapter x 3
0-10V Spindle CNC I/O Module

Shipping: $55.00

It seems to just add every shipping cost up..

bdring, 2020-10-26:
I will refund to the actual USPS First Class Package Cost.

simonemery555, 2020-10-27:
order number #223992, looking forward to the refund of postage! :P

thanks!

simonemery555, 2020-10-27:
oh and also my cnc is currently a 3 axis, with a moving bed, but i'm adding a new rotational 4th axis which is why im moving to this setup.
The XYZ axis are external nema 23 motors/drivers, the 4th is just a small nema 17 so i will just be using a small driver on board as the A axis.

bdring, 2020-10-27:
I'll probably ship it tomorrow and refund the balance.

Closing this issue. Will follow-up with email.

Closed 2020-10-27.

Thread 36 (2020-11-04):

Laser ON/OFF with CNC Relay Module

jaysettle, 2020-11-04:
I have a small 12V laser I've mounted on my gantry and I want to know if it's possible to utilize the relay module installed on slot 3 of my 6 pack to control the ON/OFF off my laser. I'd like it to work with Gcode that's written with for a laser. I don't care about laser strength in terms of the 0 to 255 scale.

I see the example code:

```
// Relay module as spindle on CNC I/O Module socket #2

#define SPINDLE_TYPE            SpindleType::RELAY // default, check actual $Spindle/Type Setting
#define SPINDLE_OUTPUT_PIN      GPIO_NUM_2 // relay as spindle on module socket #2
// Relay module as spindle on CNC I/O Module socket #3

#define SPINDLE_TYPE            SpindleType::RELAY // default, check actual $Spindle/Type Setting
#define SPINDLE_OUTPUT_PIN      GPIO_NUM_26 // relay as spindle on module socket #3

// Relay module as Mist on CNC I/O Module socket #4
#define COOLANT_MIST_PIN  GPIO_NUM_14 // Relay for Mist on module socket #4

```

However I'm questioning if it's possible to drive the laser with Gcode written for a laser. How would this be done? Thanks.

bdring, 2020-11-04:
It is a bit of a hack, but you could use it like a relay spindle.

Ideally you should use a 5v output module in laser mode.

jaysettle, 2020-11-05:
I'm ok with using the 5V output module. I can come up with some hardware relay circuit to fire the 12V laser with the 5V output module.

Question
What do I need to add in my machine file to turn on the 5V output(output 1 pin) on module slot #5 so that my gcode generated from Fusion 360 using grbl laser post processor turns it ON/OFF.

I've made an example Gcode file below. Looks like 'G0 S255 M4' turns it on and ... well, looking at the gcode I'm not sure what turns it off between circles...

```
%
(1001)
G90 G94
G17
G21

(2D Profile1)
G54
G0 S255 M4
G0 X18.6 Y-21.744
G3 X21.4 Y-18.256 Z0 I1.4 J1.744 F200
G3 X18.6 Y-21.744 I-1.4 J-1.744
G0 X17.507 Y-23.433
G3 X22.493 Y-16.567 I2.493 J3.433 F200
G3 X20 Y-15.757 I-2.493 J-3.433
G1 X19.961 Y-15.758
G3 X17.507 Y-23.433 I0.039 J-4.242
G0 X17.298 Y-24.207
G3 X25 Y-20 I2.702 J4.207 F200
G1 Y-19.969
G3 X20 Y-15 I-5 J-0.031
G3 X17.298 Y-24.207 I0 J-5
G0 X15.949 Y-25.965
G3 X20 Y-27.211 I4.051 J5.965 F200
G3 X20 Y-12.789 I0 J7.211
G3 X12.789 Y-20 I0 J-7.211
G1 Y-20.025
G3 X15.949 Y-25.965 I7.211 J0.025
G0 X14.543 Y-27.696
G3 X25.457 Y-12.304 I5.457 J7.696 F200
G3 X20 Y-10.566 I-5.457 J-7.696
G1 X19.97
G3 X10.566 Y-20 I0.03 J-9.434
G3 X14.543 Y-27.696 I9.434 J0
G0 X13.808 Y-29.309
G3 X20 Y-31.18 I6.192 J9.309 F200
G1 X20.035
G3 X31.18 Y-20 I-0.035 J11.18
G3 X8.82 Y-20 I-11.18 J0
G3 X13.808 Y-29.309 I11.18 J0
G0 X12.221 Y-32.55
G3 X27.779 Y-7.45 I7.779 J12.55 F200
G3 X20 Y-5.235 I-7.779 J-12.55
G1 X19.962
G3 X5.235 Y-20 I0.038 J-14.765
G3 X12.221 Y-32.55 I14.765 J0
G0 X11.028 Y-34.474
G3 X20 Y-37.029 I8.972 J14.475 F200
G3 X20 Y-2.971 I0 J17.029
G3 X2.971 Y-20 I0 J-17.029
G1 Y-20.056
G3 X11.028 Y-34.474 I17.029 J0.056
G1 S0
M30
%

```
Should look like this. Just some test circles. This with the laser manually wired on so it stays on. (The laser moves to the next circle so fast it appears to turn it off but it is on all the time)
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

jaysettle, 2020-11-09:
> It is a bit of a hack, but you could use it like a relay spindle.
>
> Ideally you should use a 5v output module in laser mode.

I'm trying to use the 5V module for this now per your suggestion. However I get some compile errors about "Relay" is not a spindle type. I tried "LASER" also.

My machine definition file...
```
#pragma once

#define MACHINE_NAME            "XXYZ_4XInput_4XInput_Relay_Spindle_5VOutput_ExtSteppers2"

#define N_AXIS 6

// I2S (steppers & other output-only pins)
#define USE_I2S_OUT
#define USE_I2S_STEPS
//#define DEFAULT_STEPPER ST_I2S_STATIC

#define I2S_OUT_BCK      GPIO_NUM_22
#define I2S_OUT_WS       GPIO_NUM_17
#define I2S_OUT_DATA     GPIO_NUM_21

#define X_DISABLE_PIN           I2SO(0)
#define X_DIRECTION_PIN         I2SO(1)
#define X_STEP_PIN              I2SO(2)

#define X2_DIRECTION_PIN        I2SO(4)
#define X2_STEP_PIN             I2SO(5)
#define X2_DISABLE_PIN          I2SO(7)

#define Y_DISABLE_PIN           I2SO(8)
#define Y_DIRECTION_PIN         I2SO(9)
#define Y_STEP_PIN              I2SO(10)

#define Z_DIRECTION_PIN         I2SO(12)
#define Z_STEP_PIN              I2SO(13)
#define Z_DISABLE_PIN           I2SO(15)

#define STEPPER_RESET           GPIO_NUM_19

// Socket #1
#define X_LIMIT_PIN             GPIO_NUM_33
#define Y_LIMIT_PIN             GPIO_NUM_32
#define Z_LIMIT_PIN             GPIO_NUM_35
#define PROBE_PIN               GPIO_NUM_34

// Socket #5
#define SPINDLE_TYPE            SpindleType::RELAY
#define SPINDLE_OUTPUT_PIN      I2SO(24) // No PWM
#define SPINDLE_DIR_PIN         I2SO(25)
#define COOLANT_MIST_PIN        I2SO(26)
#define COOLANT_FLOOD_PIN       I2SO(27)

// === Default settings
#define DEFAULT_STEP_PULSE_MICROSECONDS I2S_OUT_USEC_PER_PULSE
#define DEFAULT_HOMING_SQUARED_AXES bit(X_AXIS)

```

bdring, 2020-11-09:
Here are the spindle types we support.

```
enum class SpindleType : int8_t {
    NONE = 0,
    PWM,
    RELAY,
    LASER,
    DAC,
    HUANYANG,
    BESC,
    _10V,
    H2A,
};
```

They are case sensitive so it must be...

`SpindleType::RELAY`

I cut and paste the machine definition in your last post and it compiled fine for me.  in both PlatformIO and the Arduino IDE.

jaysettle, 2020-11-11:
I've loaded update grbl esp32 successfully now, but am getting an error when laser mode is enabled and I run the gcode in my post above. I'm not sure what's going on, can you help?
```
Skipping comment-only line: (%)
Skipping comment-only line: (1001)
>>> G90G94
ok
>>> G17
ok
>>> G21
ok
Skipping blank line #6
Skipping comment-only line: (2D Profile1)
>>> G54
ok
>>> G0S255M4
/home/runner/work/esp32-arduino-lib-builder/esp32-arduino-lib-builder/esp-idf/components/freertos/queue.c:1442 (xQueueGenericReceive)- assert failed!
abort() was called at PC 0x4008f9c1 on core 1
Backtrace: 0x400935e4:0x3ffd2c60 0x40093815:0x3ffd2c80 0x4008f9c1:0x3ffd2ca0 0x400f92c7:0x3ffd2ce0 0x400dc82b:0x3ffd2d00 0x400dc6f9:0x3ffd2d20 0x400dc7b5:0x3ffd2d40 0x400dcce2:0x3ffd2d60 0x400d4025:0x3ffd2d80 0x400d77fd:0x3ffd2e40 0x400d820d:0x3ffd2e60 0x400d452f:0x3ffd2fd0 0x400d2c4f:0x3ffd2ff0 0x400fad09:0x3ffd3010 0x4008fd2d:0x3ffd3030
Rebooting...
[MSG:Grbl_ESP32 Ver 1.3a Date 20201022]
[MSG:Compiled with ESP32 SDK:v3.2.3-14-gd3e562907]
[MSG:Using machine:XXYZ_4XInput_4XInput_Relay_Spindle_5VOutput_ExtSteppers2]
[MSG:Axis count 6]
[MSG:I2S Steps, Stream]
[MSG:Init Motors]
[MSG:X  Axis Standard Stepper Step:I2SO(2) Dir:I2SO(1) Disable:I2SO(0) Limits(-2357.000,0.000)]
[MSG:X2 Axis Standard Stepper Step:I2SO(5) Dir:I2SO(4) Disable:I2SO(7) Limits(-2357.000,0.000)]
[MSG:Y  Axis Standard Stepper Step:I2SO(10) Dir:I2SO(9) Disable:I2SO(8) Limits(-1213.000,0.000)]
[MSG:Z  Axis Standard Stepper Step:I2SO(13) Dir:I2SO(12) Disable:I2SO(15) Limits(-150.000,0.000)]
[MSG:Warning: Spindle output pin I2SO(24) cannot do PWM]
[MSG:Local access point GRBL_ESP started, 192.168.0.1]
[MSG:Captive Portal Started]
[MSG:HTTP Started]
[MSG:TELNET Started 23]
[MSG:Flood coolant on pin I2SO(27)]
[MSG:Mist coolant on pin I2SO(26)]
[MSG:X  Axis limit switch on pin GPIO(33)]
[MSG:Y  Axis limit switch on pin GPIO(32)]
[MSG:Z  Axis limit switch on pin GPIO(35)]
[MSG:Probe on pin GPIO(34)]
Grbl 1.3a ['$' for help]
>>> G0X18.6Y-21.744
[MSG:'$H'|'$X' to unlock]
[Error] An error was detected while sending 'G0X18.6Y-21.744': (error:9) G-code commands are locked out during alarm or jog state. Streaming has been paused.
**** The communicator has been paused ****

**** Pausing file transfer. ****

```

bdring, 2020-11-11:
I am not sure why it crashed. I cannot repeat the problem on my end.

You do have a few issues that might contributing to the problem.

[MSG:Warning: Spindle output pin I2SO(24) cannot do PWM]

None of the I2O(xx) pins can do PWM. You can only use $Spindle/Type=Relay with those pins.

It appears you are also trying to use laser mode. That should only be used with $Spindle/Type=Laser (which you cannot use)

Trying to use PWM with a relay will likely damage it.

Try fixing those 2 problems.

jaysettle, 2020-11-12:
I don’t want to use pwm for this laser, I haven’t looked into that as the what’s available to me currently from the laser is a 12v and a ground so I definitely only need discrete on and off from the 6 pack.

So is it assumed that I shouldn’t use laser mode with the I2S0(xx) pins, even though I don’t need to pwm the laser? I could move the module to another slot if that gets me the ability for gcode created for a laser to turn it on/off. Or should I just use type::spindle and keep the module where it is? Thanks.

bdring, 2020-11-12:
I  would suggest the following.

- Move the module to slot 3 or 4
- Change to $Spindle/Type=Relay

jaysettle, 2020-11-15:
Good progress. Everything works as expected with laser mode one $32=1.

The laser turned off in accordance to the bold texts below which is perfect.
```
%
(1001)
G90 G94
G17
G21

(2D Profile1)
G54
G0 S255 M4
G0 X18.6 Y-21.744
G3 X21.4 Y-18.256 Z0 I1.4 J1.744 F200
G3 X18.6 Y-21.744 I-1.4 J-1.744
**G0 X17.507 Y-23.433**
G3 X22.493 Y-16.567 I2.493 J3.433 F200
G3 X20 Y-15.757 I-2.493 J-3.433
G1 X19.961 Y-15.758
G3 X17.507 Y-23.433 I0.039 J-4.242
**G0 X17.298 Y-24.207**
G3 X25 Y-20 I2.702 J4.207 F200
G1 Y-19.969
G3 X20 Y-15 I-5 J-0.031
G3 X17.298 Y-24.207 I0 J-5
G0 X15.949 Y-25.965
G3 X20 Y-27.211 I4.051 J5.965 F200
G3 X20 Y-12.789 I0 J7.211
G3 X12.789 Y-20 I0 J-7.211
G1 Y-20.025
G3 X15.949 Y-25.965 I7.211 J0.025
**G0 X14.543 Y-27.696**
G3 X25.457 Y-12.304 I5.457 J7.696 F200
G3 X20 Y-10.566 I-5.457 J-7.696
G1 X19.97
G3 X10.566 Y-20 I0.03 J-9.434
G3 X14.543 Y-27.696 I9.434 J0
**G0 X13.808 Y-29.309**
G3 X20 Y-31.18 I6.192 J9.309 F200
G1 X20.035
G3 X31.18 Y-20 I-0.035 J11.18
G3 X8.82 Y-20 I-11.18 J0
G3 X13.808 Y-29.309 I11.18 J0
**G0 X12.221 Y-32.55**
G3 X27.779 Y-7.45 I7.779 J12.55 F200
G3 X20 Y-5.235 I-7.779 J-12.55
G1 X19.962
G3 X5.235 Y-20 I0.038 J-14.765
G3 X12.221 Y-32.55 I14.765 J0
**G0 X11.028 Y-34.474**
G3 X20 Y-37.029 I8.972 J14.475 F200
G3 X20 Y-2.971 I0 J17.029
G3 X2.971 Y-20 I0 J-17.029
G1 Y-20.056
G3 X11.028 Y-34.474 I17.029 J0.056
G1 S0
**M30**
%
```

However when I disable laser mode $32=0 and go back to cutting wood, the laser turns on and stays on, this makes sense to me I think because I have
```
$Spindle/Type=Relay
```

Is there something else I can add to the code to programmatically and truly disable the laser during $32=0 laser mode off? If not I'll add a manual override switch (I might feel better about this) so I don't burn the garage down.

bdring, 2020-11-15:
At this time the best way is to add a mechanical switch.

Currently most of the hardware setup is done when you compile the firmware. We are are working on a huge project to allow run time setup of the hardware. This will allow on the fly changes like you want. It will affect virtually every hardware type (switches, spindles, lasers, motors, etc), so it will take some time to finish.

jaysettle, 2020-11-15:
Ok this sounds great.

Hey do you guys have a donation channel?

bdring, 2020-11-15:
Thanks,

You can do a [one time donation here](https://github.com/bdring/Grbl_Esp32#donation).

You can also give a few dollars a month via the [sponsor link at the top of this page](https://github.com/bdring/Grbl_Esp32).

Closed 2020-11-22.

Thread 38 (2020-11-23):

Pre-sales I/O questions

frdfsnlght, 2020-11-23:
I apologize if this is not the correct place to ask these questions. If not, please direct me.

I'm looking to get one of these nifty controllers for an upcoming MPCNC build. I'm in the design phase and I'm trying to get a handle on wiring needs and such. Consider me fairly proficient when it comes to micro controllers/programming/electrical. The questions:

1. **Spindle/laser**
 Initially, I plan on using an off-the-shelf router with manual speed control. But I'd like to have on/off control using GRBL. Someday, I may add a "real" spindle with a VFD, and a laser. To that end, I envision using a "0-10V Spindle Module". Initially, I imagine hooking up the forward direction output to a relay to control the AC power on the router and ignoring the variable output. Obviously, moving to VFD spindle would be "easy" using this module. I imagine I could use the same forward direction signal as a "laser enable" output and of course the variable voltage to control a CC laser driver (like a BlackBuck 8M). Is this a reasonable approach? Would there be any problems using GRBL's laser mode?
1. **Endstops**
 Normally, dual endstops on an MPCNC are wired in parallel/serial such that only a single input for each axis (X/Y) is needed, usually the "X min" and "Y min" on most controllers. Assuming I'm using a "4x Input Module" for this purpose, does the 6-pack support this, or must each limit switch have a discrete input (2x X min, 2x Y min)? I'm thinking of adding limit switches on the maximum end of each axis too. Can they be wired in a similar manner to only consume a single input per axis? I'd also add an additional input module to handle min/max on the Z axis.
1. **Other inputs**
 Assuming 2 input modules as described above, I'd have 2 spare inputs. Does GRBL support pausing/resuming operation via a switch input? I imagine hooking one of the spare inputs to a switch (momentary or toggle?) and using it to pause the job, maybe to clear or check something, then resume again when pressed/toggled. Can this be done?
1. **Outputs**
 I'd like to add a "5V Output Module" and hook some of it's outputs up to relays. In particular, I'd like to hook an output up to control an air solenoid for air blast and control it with GRBL's "coolant" control. Would this be the correct way to it, or is there a more suitable GRBL control mechanism for this?

Any help would be appreciated including machine configurations, tips, or criticisms.

bdring, 2020-11-24:
In general, I would not recommend too much hacking, like using the forward direction spindle control to control the on/off. I would define everything normally and recompile when you change your system.

1.  Spindle. If you want to use the 0-10V to drive a relay You could use the forward direction circuit as a signal to a relay circuit, but I would define a SPINDLE_OUPUT_PIN to the GPIO pin going to that and use SpindleType::RELAY. You can use VFD later and redefine the pins and spindle type accordingly. I do not recommend using that module for a laser. I would get a 5V output module for that.

2. Switches. You can wire 2 switches to each input. The wiring scheme (parallel/serial) depends on whether you use N.C. or N.O. switches.

3. Other inputs: We support feedhold, resume, reset, door, probe, and 4 macro buttons.

4. Outputs. The 5V module cannot directly drive relays. It can provide a signal to a relay control circuit. The Quad MOSFET can supply the current to directly drive relays and solenoids. We support Mist and Flood as well as 4 digital output and 4 PWM outputs.

frdfsnlght, 2020-11-24:
I'm curious why you wouldn't recommend the 0-10V module to drive a laser? I would think that's a good fit. Is it because most lasers are PWM controlled (in which case, I agree with you and a 5V output module would be better)? How is the analog output derived? I took a quick look at the schematic (emphasis on "quick") and it looks like maybe you're smoothing a PWM signal and running it through an adjustable gain amp. Is that right? If that's true, is there a reason you didn't break out the PWM into another output pin on that module? Seems like a desirable enhancement. Best of both worlds.

bdring, 2020-11-24:
You are correct on the design description.

We are just trying to optimize each module, reduce confusion and keep cost
down. I tried "best of X worlds" for years. I like this system better.

On Tue, Nov 24, 2020 at 8:12 AM Tab Bennedum <notifications@github.com>
wrote:

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

--
Bart Dring

"If you did not build it, you will never own it"

jvanbrecht, 2020-12-01:
I'm looking at replacing my Xpr V4 from Spark Concepts, and I came across this today.  My main issue is currently the pwm output is fluctuating, and my spindle speed goes bonkers on anything other than full speed at 10v.  The other issue is that the spindle requires a 10 to 26V line (not sure why, everything is in German).  If I read things correctly (it's been almost 25 years since my EE degree which I never ended up using anyways), the pwm module only provides an additional 5v.. can this be boosted to 10v (the vendor that sold me the spindle stated that it just needs a voltage between 10 and 26 that is constant, does not matter what it is)

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

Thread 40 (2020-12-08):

Proximity Sensors beyond 5V

jsunday, 2020-12-08:
What is involved in getting a 6-36V or 10-30V inductive proximity sensor to work correctly?

I have a 12V power supply I can use to power the sensor, and then I would need a resistor or other electronics of some type to lower the voltage for the input of the esp32?

Thanks,

bdring, 2020-12-09:
Most proximity switches pull the signal to ground. I think if you supply the 12V to the sensor and tie the ground on sensor and the ground at the switch together it should work.

[Here is a link to Slack](https://join.slack.com/t/buildlog/shared_invite/zt-7twbithi-bRGScOaCgJoBpTbkykfxoA). The is the primary support channel for questions like this.

Closed 2021-02-02.

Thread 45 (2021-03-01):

Stepper IO-VCC vs. Shift Register VCC

EsserPrototyping, 2021-03-01:
In your schematic, there´s a jumper (J22) for logic VCC.
This is the same VCC for the stepper logic and the shift registers. If I´m right, this leads to a problem:
The datasheet of the 74AHCT595 says it needs a VCC of 4.5 to 5V. Only the 74AHC595 is compatible with 2 to 5V VCC, but it needs 3,85V logic voltage for a high input.
Is it possible to use, the TMC2130 for example, with 5V logic voltage (Step, Dir, En, Driver Logic VCC) but 3.3V on SPI and DIAG? Or maybe only Step, Dir and En with 5V and Driver Logic VCC at 3.3V? This way the 74AHCT595 could always be supplied with 5V.
I´m asking because I want to use external drives with 5V logic combined with one or two TMC2130´s.
In my case I could just put some level shifting between shift register and the stepper´s Step, Dir and En lines, but I wonder if it is necessary.

bdring, 2021-03-01:
With TMC2130, if you use 5V Vcc it will send 5V SPI and Diag to the ESP32.

Use the level shifting. If the level shifters cannot drive current on the + side, use the Vdd common jumper option.

Please ask further questions on the Discord server.

https://discord.gg/NVuTUQSgG2

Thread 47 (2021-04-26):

Problem with gcode

sns5400, 2021-04-26:
Hello, I have a older problem with a gcodefile where Bart give me before a reply but after a computer crash i do not find the solution any more. Is it possible to point me back on the rails. i remember i must modify some file before compiling the hole thing.

Gcode file:
[disk.txt](https://github.com/bdring/6-Pack_CNC_Controller/files/6375608/disk.txt)

Sreenshot:
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

Thank you in advance

bdring, 2021-04-26:
You should ask questions about Grbl_ESP32 on that repo.

https://github.com/bdring/Grbl_Esp32

You can send $e=33 to find out what error 33 is. It is an invalid target for an arc. This means you are telling Grbl to go from an existing location to a new location via a specific arc move. When Grbl calculates that arc move it does not get exactly to that target.

This could be due to the fact that your gcode is not very accurate with only 2 decimal places. You should try to get your CAM program to generate more accuracy. This will insure the best accuracy.

Another way is to allow more tolerance in Grbl. Arc tolerance is set via the $GCode/ArcTolerance setting. The default is 0.002mm. You can see it is very likely that 2 decimal places will produce an error. I would think that **$GCode/ArcTolerance=0.03** would work.

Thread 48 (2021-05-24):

Removable power supply module

keax, 2021-05-24:
Hello,

First of all, many thanks for your great job !
I have the V1p5 board version and I have a problem to find the AP64350SP-13 component (it's out of stock or with expensive shipping cost) and I don't find any good replacement. In the V1p8, you use the TPS54360DDAR instead, which looks great...but once again, it's out of stock. I think I found a valid replacement : TPS54560DDAR.
So for now, as AP64350SP-13 is not replaceable by TPS54560DDAR, I can order the V1p8 or create a dirty specific power supply module I will plug on FAN connector (with VMot and 5V) to supply 5V from VMot.

But maybe the best answer is to convert the power supply part to a removable (and upgradable) power supply module ?

bdring, 2021-05-24:
The current electronics shortage makes a lot of parts hard to get.

I have used plug in power supplies in the past.

Dan018, 2021-07-03:
I was going to post the exact same comment. The availability of chips has made several items hard to get. I reworked the PCB to accept one of these as the power supply.

https://m.aliexpress.com/item/4000938525410.html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

It would be easy enough to create a module that uses the same pinout but uses whatever components you like (or are available). Imo it would also provide some futureproofing for when components reach EOL.

StephS, 2021-12-28:
It would be easy enough to do both. Have the footprint for the onboard supply, but a header to use a module.
Pololu sells high quality modules. But their pinout is not consistent between models.
https://www.pololu.com/product/2858
I think 5 pin, Vout, GND, Vin, En, PowerGood covers all of the use cases. Then the user can adapt the pins as needed.
Due to the different sizes and pinouts, a mounting hole would be difficult, but a protoboard intermediate might be an option.

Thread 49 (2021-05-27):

Quad_Basic_Input_v1p1

trafoman2004, 2021-05-27:
About the Quad_Basic_Input_v1p1 is it outputting 5V directly to the ESP32 inputs, is that right?

truglodite, 2021-06-12:
Yes I observed the same problem with the schematic. I mentioned it a while back in discord, but just heard crickets afterwards. I think the gist is most ppl are buying the opto isolated boards, and folks making DIY input boards probably make up the majority of users who are stumbling upon this particular problem. Nonetheless, it should be fixed.

I used my cnc to cut my own expansion boards for my 6-pack. So I was able to revise the circuit with an added 3v3 LDO to power the chip. I had a bunch of spare AMS1117-3.3 on hand so just used those. The original schematic and board files could easily be updated to use any old LDO, but more caps would also be required.

Since my use required 3x quad input boards, I ended up using an LDO on each board for convenience. It would have been easy to add jumpers and use one LDO to power all 3 input chips, but I chose not to as that makes it too wirey for me. With this in mind, I was wondering if the 6-pack could be revised to have 3v3 on the mainboard, and change the expansion pinouts to use this 3v3 in case it's needed. For example, the p12-p15 pins exist on all the expansion headers, but from what I can see there doesn't seem to be any available module that makes use of them. I figure that may be for dev or future use, but if not maybe one of those could be used for 3v3?

StephS, 2021-12-28:
In this case it's likely better to have the 3.3v voltage regulator on the expansion board, because the 3.3v is being generated on the ESP32 board and not the 6-Pack control board. The supply from the ESP32 varies in current rating, but to isolate noise on the MCU it's best it uses a different supply. A small size low cost linear regulator could be used.

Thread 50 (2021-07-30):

Can't control BESC spindle.

Iron-Dan, 2021-07-30:
Hello everybody,

I wanted to drive a brushless motor with the 6-Pack CNC Controller and installed RC Servo/BESC CNC I/O Module on socket #4.
I programmed the BESC with a servo tester and then
wanted to drive it with the controller, but it didn't work.
The motor was only beeping and not turning, so I compared the PWM signals of the servo tester and the RC Servo/BESC CNC I/O Module with the scope. I found out that GPIO14 delivered the correct pulse widths at commands S0 (1ms) and S1000 (2ms), but the voltage level is about factor 10 too low. The voltage level of the pulses at GPIO14 are just 0.56V, at the servo tester they are 5V.

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

Does anybody know why the ESP32 delivers such a low voltage, shouldn't it be 3.3V?
How can I fix this?

Thanks and best regards,
Dan

bdring, 2021-07-30:
Have you tried measuring with with no servo attached? Can you try it with a different pin.

You could have a damaged or overloaded pin.

Iron-Dan, 2021-07-31:
Hi bdring,Thank you for the fast Response.I checked it with another ESP32 and I could control a SG90 servo. My scope at home doesn't work, I will check the signal at work on monday. The BESC is also at work, so I can't check it now. ☹️But it seems like the other ESP has a defective port.Best regards,Dan-- Diese Nachricht wurde von meinem Android Mobiltelefon mit WEB.DE Mail gesendet.Am 30.07.21, 16:47 schrieb bdring ***@***.***>:

  Have you tried measuring with with no servo attached? Can you try it with a different pin.
  You could have a damaged or overloaded pin.
  —You are receiving this because you authored the thread.Reply to this email directly, view it on GitHub, or unsubscribe.

Iron-Dan, 2021-08-01:
Hi bdring,

I got my scope at home running and now I can confirm that everything seems ok at the second ESP32, the voltage level is now 3.3V.

Command S0:
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

Command S1000:
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

I have another question about the spindle buttons in the WebUI.
Do they only work when a job is running or should I be able to turn the spindle on and off at any time?
I'm wondering because the mist button is working at any time.

At last I would say thank you for the good job at ESP32_GRBL and 6-Pack CNC Controller, they are really cool.
I have sent you a 20$ donation via Paypal.

Thanks and best regards,
Dan

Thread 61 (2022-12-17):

how to properly operate relay switch and enable them

erikcramerjr, 2022-12-17:
hi,
ive used install-fs from version fluidnc-v3.6.5-win64 to install the firmware and added the following config :

[config.txt](https://github.com/bdring/6-Pack_CNC_Controller/files/10251582/config.txt)
To enable the relays ive placed them on module 3 and 4, i intend to use one for the spindle and one for the vacuum.
In the near future i might use one also for compressed air.
and and a lcd and opto for the sensors

to enable the relays i have Unlocked the machine (clear alarm)
Then i pressed the spindle, flood , mist buttons but these dont do any thing.
So i thought i must use the device M6 T0 or T1
So i noticed that under tool_num  both devices have numer 100 so i changed these to 0 and 1 and tested again, with the same result. (i expect a click from the relay and the LEd to light up)

Do i need to compile the firmware to get this working correctly

Or do i have to use some thing like this with the relay for the vacuum  Because i thested this but it also didnt work?
 coolant:
  flood_pin: gpio.14
  mist_pin: NO_PIN
  delay_ms: 0

Verbose log from enabling the pins
$G
[MSG:VRB: Cannot open file /spiffs/macrocfg.json]
[MSG:VRB: Cannot open file /spiffs/macrocfg.json.gz]
[MSG:VRB: Cannot open file /spiffs/404.htm]
[MSG:VRB: Cannot open file /spiffs/404.htm.gz]
<Alarm|MPos:0.000,0.000,0.000|FS:0,0|Pn:YZ|WCO:0.000,0.000,0.000>
<Alarm|MPos:0.000,0.000,0.000|FS:0,0|Pn:YZ|Ov:100,100,100>
$X
<Alarm|MPos:0.000,0.000,0.000|FS:0,0|Pn:YZ>
[MSG:INFO: Caution: Unlocked]
ok
<Idle|MPos:0.000,0.000,0.000|FS:0,0|Pn:YZ>
<Idle|MPos:0.000,0.000,0.000|FS:0,0|Pn:YZ>
<Idle|MPos:0.000,0.000,0.000|FS:0,0|Pn:YZ>
<Idle|MPos:0.000,0.000,0.000|FS:0,0|Pn:YZ>
<Idle|MPos:0.000,0.000,0.000|FS:0,0|Pn:YZ>
<Idle|MPos:0.000,0.000,0.000|FS:0,0|Pn:YZ>
<Idle|MPos:0.000,0.000,0.000|FS:0,0|Pn:YZ>
<Idle|MPos:0.000,0.000,0.000|FS:0,0|Pn:YZ|WCO:0.000,0.000,0.000>
<Idle|MPos:0.000,0.000,0.000|FS:0,0|Pn:YZ|Ov:100,100,100>
<Idle|MPos:0.000,0.000,0.000|FS:0,0|Pn:YZ>
<Idle|MPos:0.000,0.000,0.000|FS:0,0|Pn:YZ>
m7
<Idle|MPos:0.000,0.000,0.000|FS:0,0|Pn:YZ>
ok
m8
<Idle|MPos:0.000,0.000,0.000|FS:0,0|Pn:YZ>
ok
<Idle|MPos:0.000,0.000,0.000|FS:0,0|Pn:YZ>
<Idle|MPos:0.000,0.000,0.000|FS:0,0|Pn:YZ>
m6 T0
[MSG:INFO: Tool No: 0]
[MSG:INFO: Using spindle Relay]
ok
<Idle|MPos:0.000,0.000,0.000|FS:0,0|Pn:YZ|Ov:100,100,100>
<Idle|MPos:0.000,0.000,0.000|FS:0,0|Pn:YZ>
M6 T1
[MSG:INFO: Tool No: 1]
[MSG:INFO: Using spindle Relay]
ok
Image of relay settings, (when i have both relay settings in there like in the config they both show up., this is a screenshot with only one and the other settings was with Coolant option)
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
For coolant i can only find this one setting:
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

bdring, 2022-12-17:
The buttons on the Webui are overrides. Send M7, M8 and M9 from the console.

erikcramerjr, 2022-12-17:
Thank you Module 4 switches like a Charm

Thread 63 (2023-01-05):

No Source file for 0-10V spindle

abrackers, 2023-01-05:
Thanks for all of your work on this. I noticed there was no Source file available for the 0-10v spindle module, while all of the other modules had diptrace (or in one case kicad) source files. Would it be possilble for you to provide the source file for the 0-10v spindle module? Thanks

bdring, 2023-01-05:
Here is the most current version.

https://oshwlab.com/bdring/10v-spindle-cnc-i-o-module

abrackers, 2023-01-07:
Thanks, I hadn't found that site yet

Closed 2023-01-07.

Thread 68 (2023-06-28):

6-pack-external motors not moving

oscarjoker7, 2023-06-28:
I’ve got the new 6 pack with external drivers. I have everything wired and programmed but motors are not turning. I am using dm542 drivers

jvanbrecht, 2023-07-01:
You have asimilar setup as mine, but will need a lot more information.
1. are you sure you have the motors wired correctly, check the pairs, tie them together, if there is no resistance to manual rotation, they are wired wrong.
2. Which 6 pack do you have, there are 2, one with modules, one just for external drivers.  (not sure if this makes a difference, I have the one with the modules for external drivers, not the one that has those built in, but cannot hurt to know, not sure if the pinouts are the same)
3. Post your configuration file
4. What other modules do you have (for example I have the two 4 input, 0-10v spindle driver)

These would be a good place to start.

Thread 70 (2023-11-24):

Just an Observation with Probe definition and gpio

Bill83046, 2023-11-24:
In configuration files for probe: I find that it does not conform to other definitions of gpios.
probe:
  pin: gpio.25
examples:
      limit_neg_pin:  gpio
      limit_pos_pin:  gpio
      limit_all_pin:
I would expect it to be as below to follow other gpio definitions.
probe:
probe_pin: gpio
Do not know if this was intentional or just an overlook. Am I reading this correctly?
Previous iterations have probe_pin: gpio
Bill Roberts

bdring, 2023-11-24:
I don't follow your question. Here is the wiki page.

http://wiki.fluidnc.com/en/config/probe

Here is an example

```yaml
probe:
  pin: gpio.34
  toolsetter_pin: gpio.14
  check_mode_start: true
  ```

  Initially there was only one pin. That is why the 2 pins look a little different.

Bill83046, 2023-11-24:
All of your gpio definitions have mostly the same format, i.e. name_pin: gpio#. The probe: gpio# definition strays from that format ( a  housekeeping issue with me, I just like to see things defined in the same manner). Just an observation on my part. I know it probably does not make a difference.  I am trying to track down an issue with a probe error not being defined when I upgraded to v3.70.10. I Reverted back to V3.7.9 and is ok. Do not know if it is me yet? When I get to installing 3.70.1 again I will keep track of messages and errors and if necessary, update with issue.

bdring, 2023-11-25:
There are a few items that broke our naming convention. Many things and sections evolved over time. There are many things we would love to change, but breaking thousands of working config files would be a support nightmare.

Bill83046, 2023-11-28:
I get it. I was a controls engineer for Jet Engine Component test stands for 23 years. The controls software that I used and developed was for only one person, not the many that you try to make happy. But you understand where I am coming from. I tend to ask a lot of questions if I do not understand or if you will, question the methods.
Now running V3.70.1 . I get 2 messages  [MSG:DBG: /macrocfg.json not found] and [MSG:DBG: 404.htm not found]
I assume this has to do with the WEB EUI. Do not know why but it dose not effect the operation so far. Cannot find any details on this on the WEB.
So far so good my machine is up and running except for VFD Spindleand that is next.  All axises are calibrated accurate and repeatable.
Thanks
Bill Roberts

bdring, 2023-11-28:
If you have questions about FluidNC, it is better to ask on the FluidNC github repo. More people will see it there.

We also have a Discord server with a WebUI channel.

https://discord.gg/az5DaQS9

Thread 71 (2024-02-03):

6 pack built in esp, motors don't move

Kevycnc, 2024-02-03:
I have a 6 pack controller that I have gone over the wiring multiple times.  Had a friend also look at it. to confirm.  I seem to have everything hooked up correctly. I can Enable and disable the motors with commands.  However if I try to jog any, they all lock up and of course nothing moves.   This was purchased on Tindie order 442504.  Hoping I can get assistance with the correct config to start.

One other weird thing I noticed on the board.  I have 3 axis wired up.  But for some reason the ENA led on what would be Motor 5 (Ena I2SO.16 from the pinout on the wiki) is always lit when the controller is powered on.

Thanks.

I do suspect most of  its because of my config file as I have struggled with it and tried a few while making changes to suit.  I see one alarm mentioned at the end.  I try to clear prior to jogging. Should note I currently have no limit switches set up.

My Startup messages:
$ss
[MSG:INFO: FluidNC 3.7.13 https://github.com/bdring/FluidNC]]
[MSG:INFO: Compiled with ESP32 SDK:v4.4.4]]
[MSG:INFO: Local filesystem type is spiffs]]
[MSG:INFO: Configuration file:config.yaml]]
[MSG:INFO: Machine 6 Pack External XYZ]]
[MSG:INFO: Board 6 Pack]]
[MSG:INFO: I2SO BCK:gpio.22 WS:gpio.17 DATA:gpio.21]]
[MSG:INFO: SPI SCK:gpio.18 MOSI:gpio.23 MISO:gpio.19]]
[MSG:INFO: SD Card cs_pin:gpio.5 detect:NO_PIN freq:8000000]]
[MSG:INFO: Stepping:I2S_stream Pulse:4us Dsbl Delay:0us Dir Delay:1us Idle Delay:250ms]]
[MSG:INFO: Axis count 3]]
[MSG:INFO: Axis X (0.000,730.000)]]
[MSG:INFO:   Motor0]]
[MSG:INFO:     stepstick Step:I2SO.2 Dir:I2SO.1 Disable:I2SO.0]]
[MSG:INFO:  X Neg Limit gpio.33]]
[MSG:INFO:  X Pos Limit gpio.32]]
[MSG:INFO: Axis Y (-880.000,0.000)]]
[MSG:INFO:   Motor0]]
[MSG:INFO:     stepstick Step:I2SO.5 Dir:I2SO.4 Disable:I2SO.7]]
[MSG:INFO:  Y Neg Limit gpio.35]]
[MSG:INFO:  Y Pos Limit gpio.34]]
[MSG:INFO: Axis Z (-50.000,0.000)]]
[MSG:INFO:   Motor0]]
[MSG:INFO:     standard_stepper Step:I2SO.10 Dir:I2SO.9 Disable:I2SO.8]]
[MSG:INFO:  Z Neg Limit gpio.2]]
[MSG:INFO:  Z Pos Limit gpio.25]]
[MSG:INFO: Kinematic system: Cartesian]]
[MSG:INFO: Using spindle NoSpindle]]
[MSG:INFO: STA SSID is not set]]
[MSG:INFO: AP SSID FluidNC IP 192.168.0.1 mask 255.255.255.0 channel 1]]
[MSG:INFO: AP started]]
[MSG:INFO: WiFi on]]
[MSG:INFO: Captive Portal Started]]
[MSG:INFO: HTTP started on port 80]]
[MSG:INFO: Telnet started on port 23]]
ok
<Alarm|MPos:0.000,0.000,0.000|FS:0,0|Pn:XY|WCO:0.000,0.000,0.000>

```yaml
board: 6 Pack
name: 6 Pack External XYZ
meta: Kev Setup

stepping:
  engine: I2S_STREAM
  idle_ms: 250
  pulse_us: 4
  dir_delay_us: 1
  disable_delay_us: 0

axes:
  shared_stepper_disable_pin: NO_PIN
  x:
    steps_per_mm: 100.000
    max_rate_mm_per_min: 5000.000
    acceleration_mm_per_sec2: 50.000
    max_travel_mm: 730.000
    soft_limits: false
    homing:
      cycle: 2
      positive_direction: false
      mpos_mm: 0.000
      feed_mm_per_min: 100.000
      seek_mm_per_min: 200.000
      settle_ms: 500
      seek_scaler: 1.100
      feed_scaler: 1.100

    motor0:
      limit_neg_pin: gpio.33
      limit_pos_pin: gpio.32
      limit_all_pin: NO_PIN
      hard_limits: false
      pulloff_mm:1.000
      stepstick:
        ms3_pin: i2so.3
        step_pin: I2SO.2
        direction_pin: I2SO.1
        disable_pin: I2SO.0

  y:
    steps_per_mm: 100.000
    max_rate_mm_per_min: 5000.000
    acceleration_mm_per_sec2: 50.000
    max_travel_mm: 880.000
    soft_limits: false
    homing:
      cycle: 2
      positive_direction: true
      mpos_mm: 0.000
      feed_mm_per_min: 100.000
      seek_mm_per_min: 200.000
      settle_ms: 500
      seek_scaler: 1.100
      feed_scaler: 1.100

    motor0:
      limit_neg_pin: gpio.35
      limit_pos_pin: gpio.34
      limit_all_pin: NO_PIN
      hard_limits: false
      pulloff_mm:1.000
      stepstick:
        ms3_pin: i2so.6
        step_pin: I2SO.5
        direction_pin: I2SO.4
        disable_pin: I2SO.7

  z:
    steps_per_mm: 100.000
    max_rate_mm_per_min: 5000.000
    acceleration_mm_per_sec2: 50.000
    max_travel_mm: 50.000
    soft_limits: false
    homing:
      cycle: 2
      positive_direction: true
      mpos_mm: 0.000
      feed_mm_per_min: 100.000
      seek_mm_per_min: 200.000
      settle_ms: 500
      seek_scaler: 1.100
      feed_scaler: 1.100

    motor0:
      limit_neg_pin: gpio.2
      limit_pos_pin: gpio.25
      limit_all_pin: NO_PIN
      hard_limits: false
      pulloff_mm:1.000
      standard_stepper:
        step_pin: I2SO.10
        direction_pin: I2SO.9
        disable_pin: I2SO.8

i2so:
  bck_pin: gpio.22
  data_pin: gpio.21
  ws_pin: gpio.17

spi:
  miso_pin: gpio.19
  mosi_pin: gpio.23
  sck_pin: gpio.18

sdcard:
  card_detect_pin: NO_PIN
  cs_pin: gpio.5

bdring, 2024-02-03:
- What stepper motor drivers are you using?
- How are your jumper configured?

If you only use i2so numbers less than 16 the controller is not actively setting the higher i2so number values.

Kevycnc, 2024-02-03:
HI, the stepper drivers are  DM556T for Y axis, DM542T for X and Z axis.  I am unclear what you mean about the jumper configuration.  I will attach some pictures.

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

bdring, 2024-02-04:
That is not technically a 6 Pack. It is a 6x which does not have the plug in modules. No jumpers to worry about on this controller.

- Do the step LEDs light dimly when you try to move?
- Try changing the pulse_ms to 8 or 12.

Kevycnc, 2024-02-04:
Hi, apologies for the confusion on the board type.
The step LED's do show dim when trying to move. Other motor LED's go off until what I assume is the command completing,
I tried to change the  Pulse_us setting to 12 and then 8 ( I didn't see a pulse_ms in the file).  At 8 it seemed the Step LED's were brighter when trying to move, but still no success. The appropriate step LED dimly lights, however it appears all motors lock whenever I send a jog command.  Even though I only attempt to jog one axis at a time.

Appreciate the help on this.

bdring, 2024-02-04:
If the correct step LEDs glow during the motion, the controller is setup right.

The signal that goes to the LED also goes to the driver.

Are you sure the driver switches are right?

bdring, 2024-02-04:
All motors lock during any motion.

Many people will set `idle_ms: 255` to keep motors locked at all times. This prevents drift between moves. You can always unlock with `$MD` or `$MD=<axes>`

Kevycnc, 2024-02-04:
Hi, that makes sense on the motors locking up.  I have went through the  driver switches, rechecked motor and controller wiring and all seems good. Lights all proper when sending commands or trying to jog,  except for the one that's not even in use.  I am still concerned why there is the one random LED lit all the time on the motor 5 ENA led.  Is this a problem?

Currently my motor drives are set to proper current for each motor.  And they are set to microstep 4  which is 800 steps/rev.
I changed my Yaml file in an attempt to get things moving.  Im  am a total noob at this Yaml so it could be something in my setup so far.  I know on Tindie it was offered to have a file setup based on some information sent. I didn't do it at the time as I wasn't sure yet.  I don't mid learning and trying, but wondering if I am fighting against it as well.

```yaml
board: 6 Pack
name: 6 Pack External XYZ
meta: Kev Setup

stepping:
  engine: I2S_STREAM
  idle_ms: 250
  pulse_us: 4
  dir_delay_us: 5
  disable_delay_us: 0

axes:
  shared_stepper_disable_pin: NO_PIN
  x:
    steps_per_mm: 20
    max_rate_mm_per_min: 100.000
    acceleration_mm_per_sec2: 25.000
    max_travel_mm: 730.000
    soft_limits: false

    motor0:
     standard_stepper:
        step_pin: I2SO.2
        direction_pin: I2SO.1
        disable_pin: I2SO.0

  y:
    steps_per_mm: 20
    max_rate_mm_per_min: 100.000
    acceleration_mm_per_sec2: 25.000
    max_travel_mm: 880.000
    soft_limits: false

    motor0:
      standard_stepper:
        step_pin: I2SO.5
        direction_pin: I2SO.4
        disable_pin: I2SO.7

  z:
    steps_per_mm: 20.000
    max_rate_mm_per_min: 100.000
    acceleration_mm_per_sec2: 25.000
    max_travel_mm: 50.000
    soft_limits: false

    motor0:
      standard_stepper:
        step_pin: I2SO.10
        direction_pin: I2SO.9
        disable_pin: I2SO.8

i2so:
  bck_pin: gpio.22
  data_pin: gpio.21
  ws_pin: gpio.17

spi:
  miso_pin: gpio.19
  mosi_pin: gpio.23
  sck_pin: gpio.18

sdcard:
  card_detect_pin: NO_PIN
  cs_pin: gpio.5

Startup still no errors
$ss
[MSG:INFO: FluidNC 3.7.13 https://github.com/bdring/FluidNC]]
[MSG:INFO: Compiled with ESP32 SDK:v4.4.4]]
[MSG:INFO: Local filesystem type is spiffs]]
[MSG:INFO: Configuration file:config.yaml]]
[MSG:INFO: Machine 6 Pack External XYZ]]
[MSG:INFO: Board 6 Pack]]
[MSG:INFO: I2SO BCK:gpio.22 WS:gpio.17 DATA:gpio.21]]
[MSG:INFO: SPI SCK:gpio.18 MOSI:gpio.23 MISO:gpio.19]]
[MSG:INFO: SD Card cs_pin:gpio.5 detect:NO_PIN freq:8000000]]
[MSG:INFO: Stepping:I2S_stream Pulse:4us Dsbl Delay:0us Dir Delay:5us Idle Delay:250ms]]
[MSG:INFO: Axis count 3]]
[MSG:INFO: Axis X (-730.000,0.000)]]
[MSG:INFO:   Motor0]]
[MSG:INFO:     standard_stepper Step:I2SO.2 Dir:I2SO.1 Disable:I2SO.0]]
[MSG:INFO: Axis Y (-880.000,0.000)]]
[MSG:INFO:   Motor0]]
[MSG:INFO:     standard_stepper Step:I2SO.5 Dir:I2SO.4 Disable:I2SO.7]]
[MSG:INFO: Axis Z (-50.000,0.000)]]
[MSG:INFO:   Motor0]]
[MSG:INFO:     standard_stepper Step:I2SO.10 Dir:I2SO.9 Disable:I2SO.8]]
[MSG:INFO: Kinematic system: Cartesian]]
[MSG:INFO: Using spindle NoSpindle]]
[MSG:INFO: STA SSID is not set]]
[MSG:INFO: AP SSID FluidNC IP 192.168.0.1 mask 255.255.255.0 channel 1]]
[MSG:INFO: AP started]]
[MSG:INFO: WiFi on]]
[MSG:INFO: Captive Portal Started]]
[MSG:INFO: HTTP started on port 80]]
[MSG:INFO: Telnet started on port 23]]
ok
<Idle|MPos:0.000,0.000,0.000|FS:0,0|WCO:0.000,0.000,-50.000>

Thanks again.

Kevycnc, 2024-02-05:
Success!  I'm an idiot. It was a driver setting/switch.  For future reference for anyone who missed it like me, they were set to 24V and I completely missed the switch to 5V.  So now I believe I can adjust the yaml file to get it where I need.

I am still wondering about the random LED that's lit.  Perhaps a bad LED?

Thanks for the assistance.

bdring, 2024-02-05:
I think the LED might turn off if you use anything in the 16-31 range. Try adding this or change the number to the actual offending LED pin number.

```yaml
user_outputs:
  digital0_pin: i2so.16
```

bdring, 2024-02-05:
The LEDs actually helped a lot here, because we knew the problem was outside the controller.

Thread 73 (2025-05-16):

Esp32 µC getting fried by the 6pack board.

crasu, 2025-05-16:
I have used my 6pack v1p8 for a couple of years now with my mpcnc. I have got a display and to 4xInput modules.

Recently the 6pack started eating µCs. Today I got really bad an I had to replace the esp32 on the board two times and about 2-3 times in the last year. In all cases the voltage regulator on the esp32 boards are fried. I have tried different esp32 boards. I checked the power supply, pin for the esp32 - They are at 5V. I use wifi and have no usb cable connected to the board.

Are there any known issues with the board that could cause this? Any ideas?

bdring, 2025-05-16:
It is usually due to pulling too much 3.3v from the esp32 module. That heats up the regulator.

crasu, 2025-05-17:
Thank your for your quick response! Any idea how to debug this? I already checked the esp32 with an ohm meter for shorts against ground (nothing). Last year I swapped all stepper drivers (drv8825).

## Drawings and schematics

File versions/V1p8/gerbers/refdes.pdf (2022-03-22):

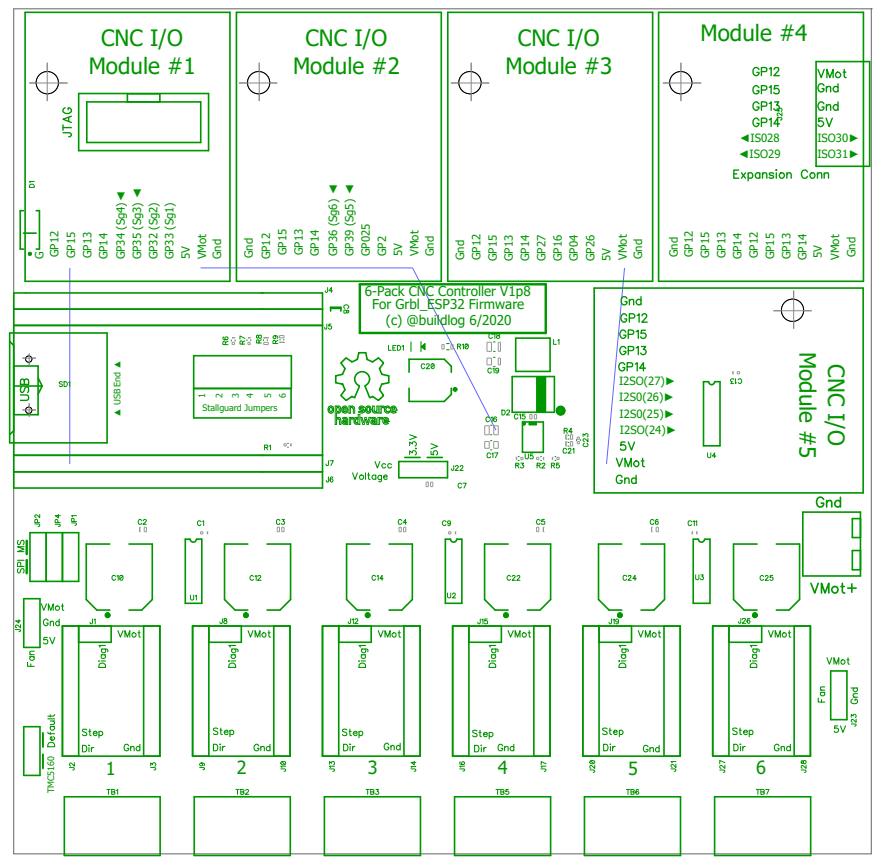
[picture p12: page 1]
Stallguard Jumpers; TMC5160; VMot; Gnd; CNC I/O Module #1; CNC I/O Module #2; CNC I/O Module #3; Module #4; CNC I/O; Module #5; ▲ USB End ▲; ◄ISO29; ISO31►; ISO30►

6-Pack CNC Controller V1p8
For Grbl_ESP32 Firmware
(c) @buildlog 6/2020

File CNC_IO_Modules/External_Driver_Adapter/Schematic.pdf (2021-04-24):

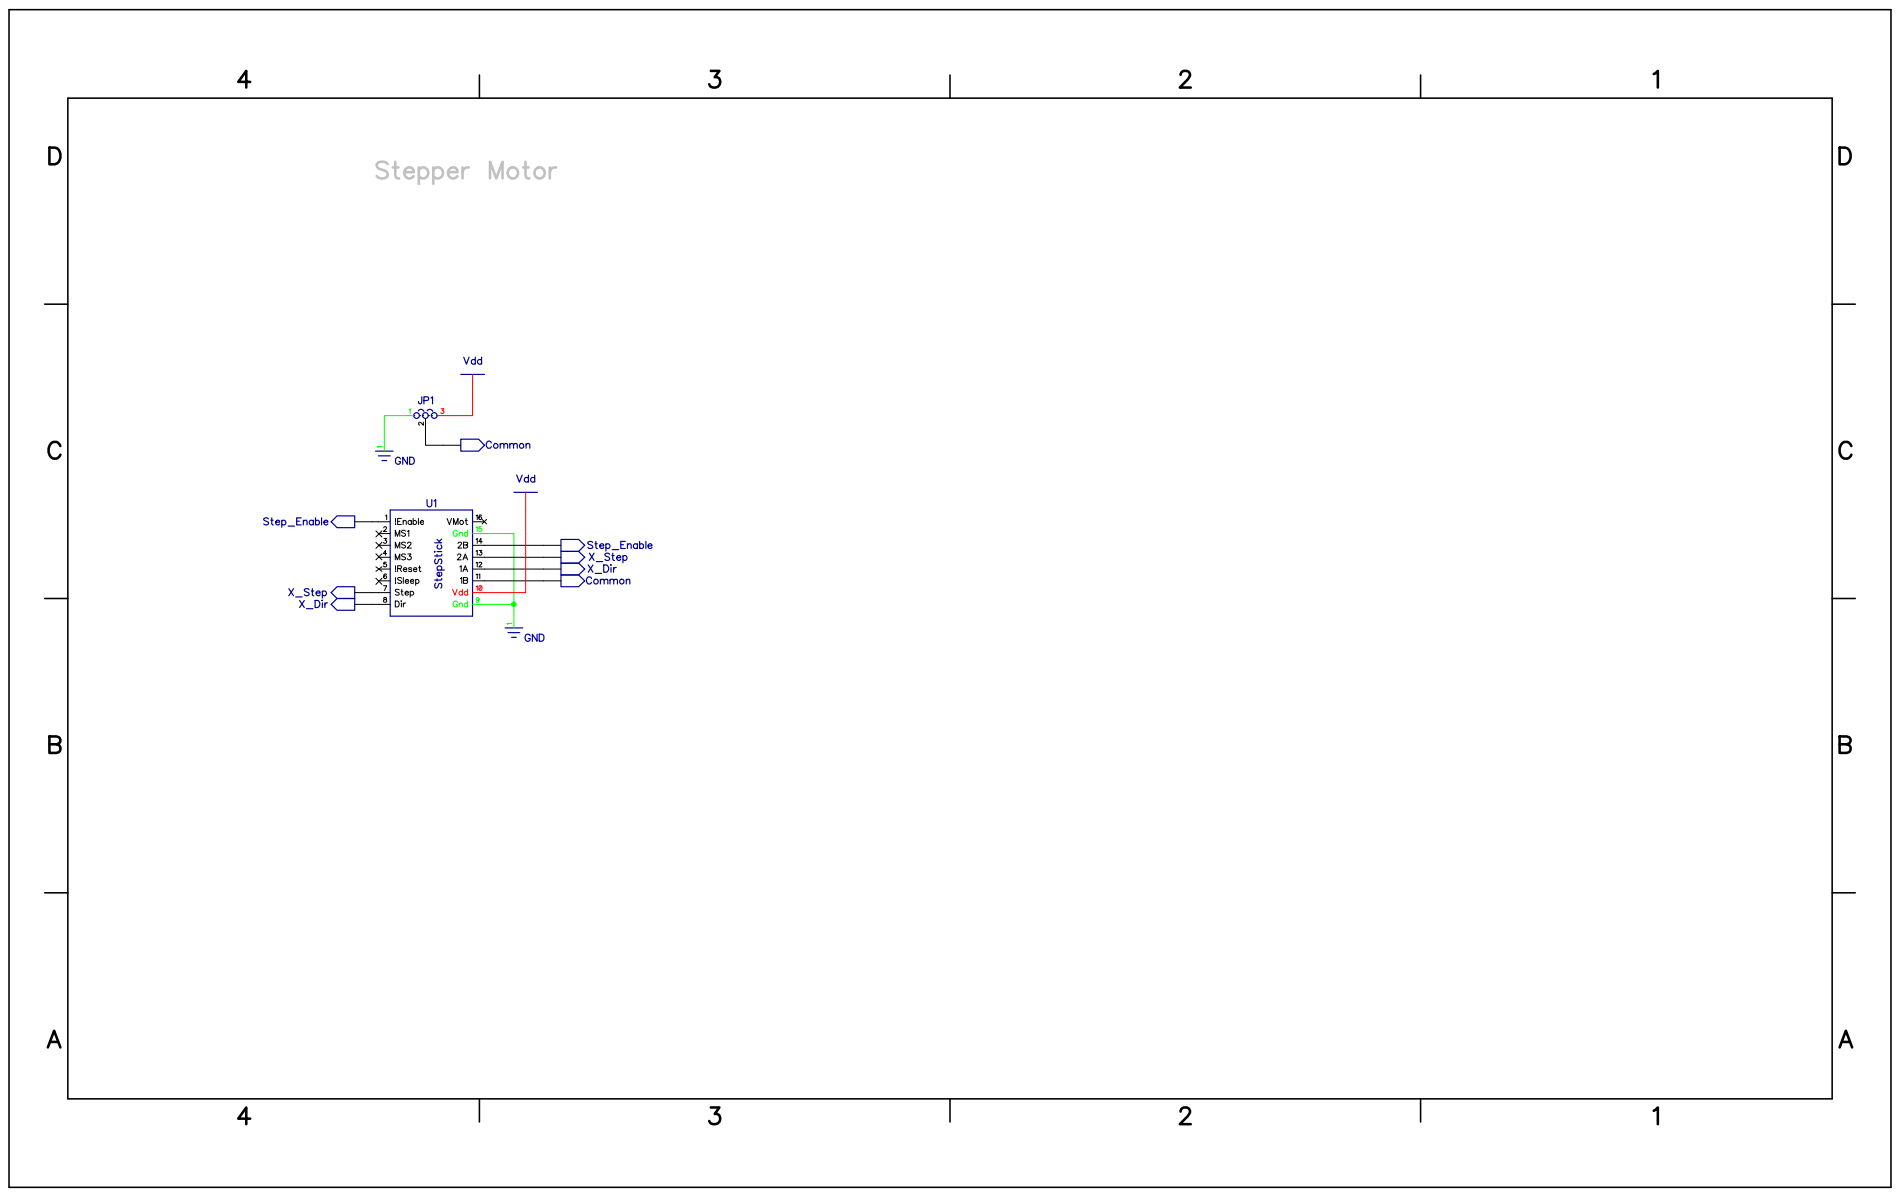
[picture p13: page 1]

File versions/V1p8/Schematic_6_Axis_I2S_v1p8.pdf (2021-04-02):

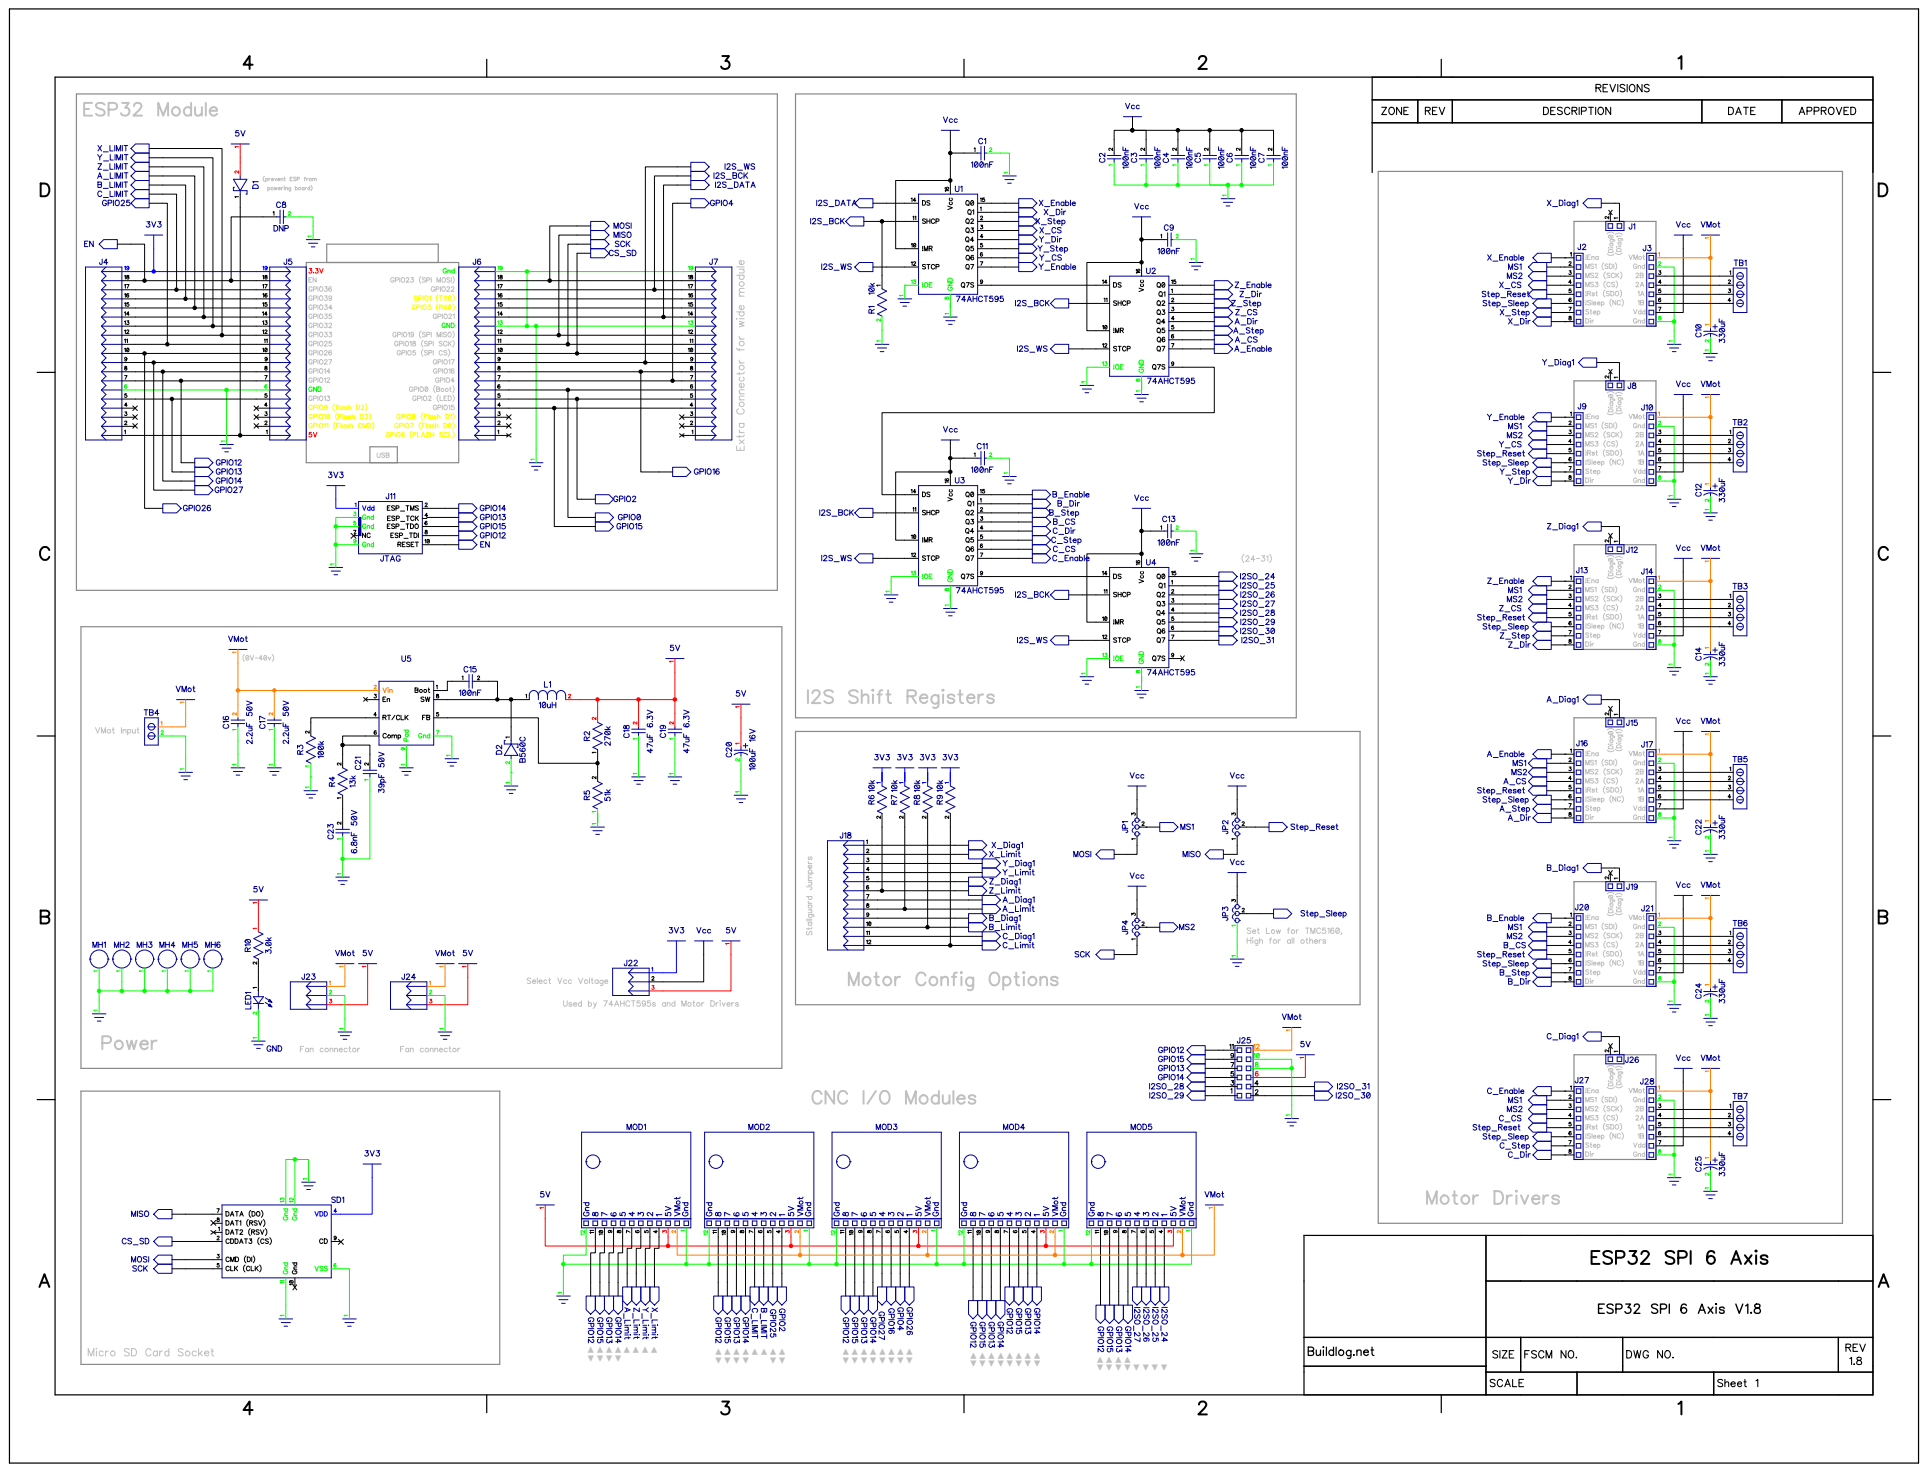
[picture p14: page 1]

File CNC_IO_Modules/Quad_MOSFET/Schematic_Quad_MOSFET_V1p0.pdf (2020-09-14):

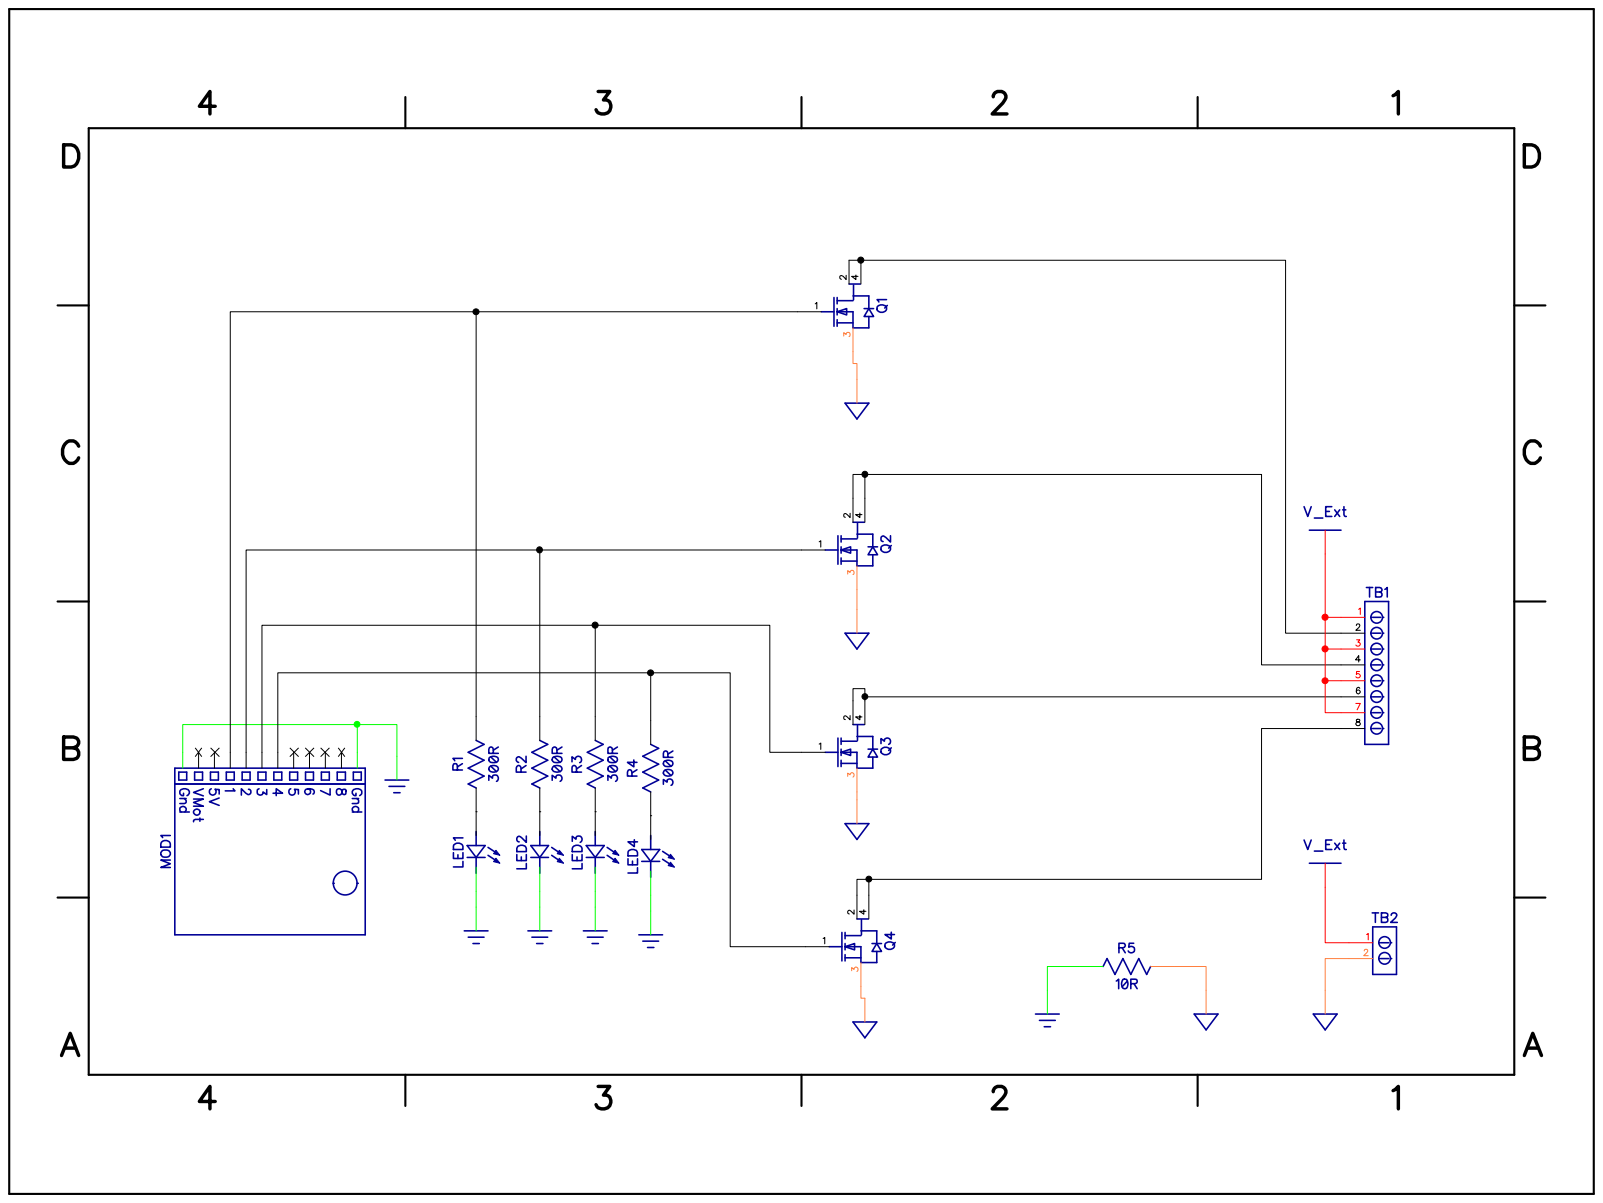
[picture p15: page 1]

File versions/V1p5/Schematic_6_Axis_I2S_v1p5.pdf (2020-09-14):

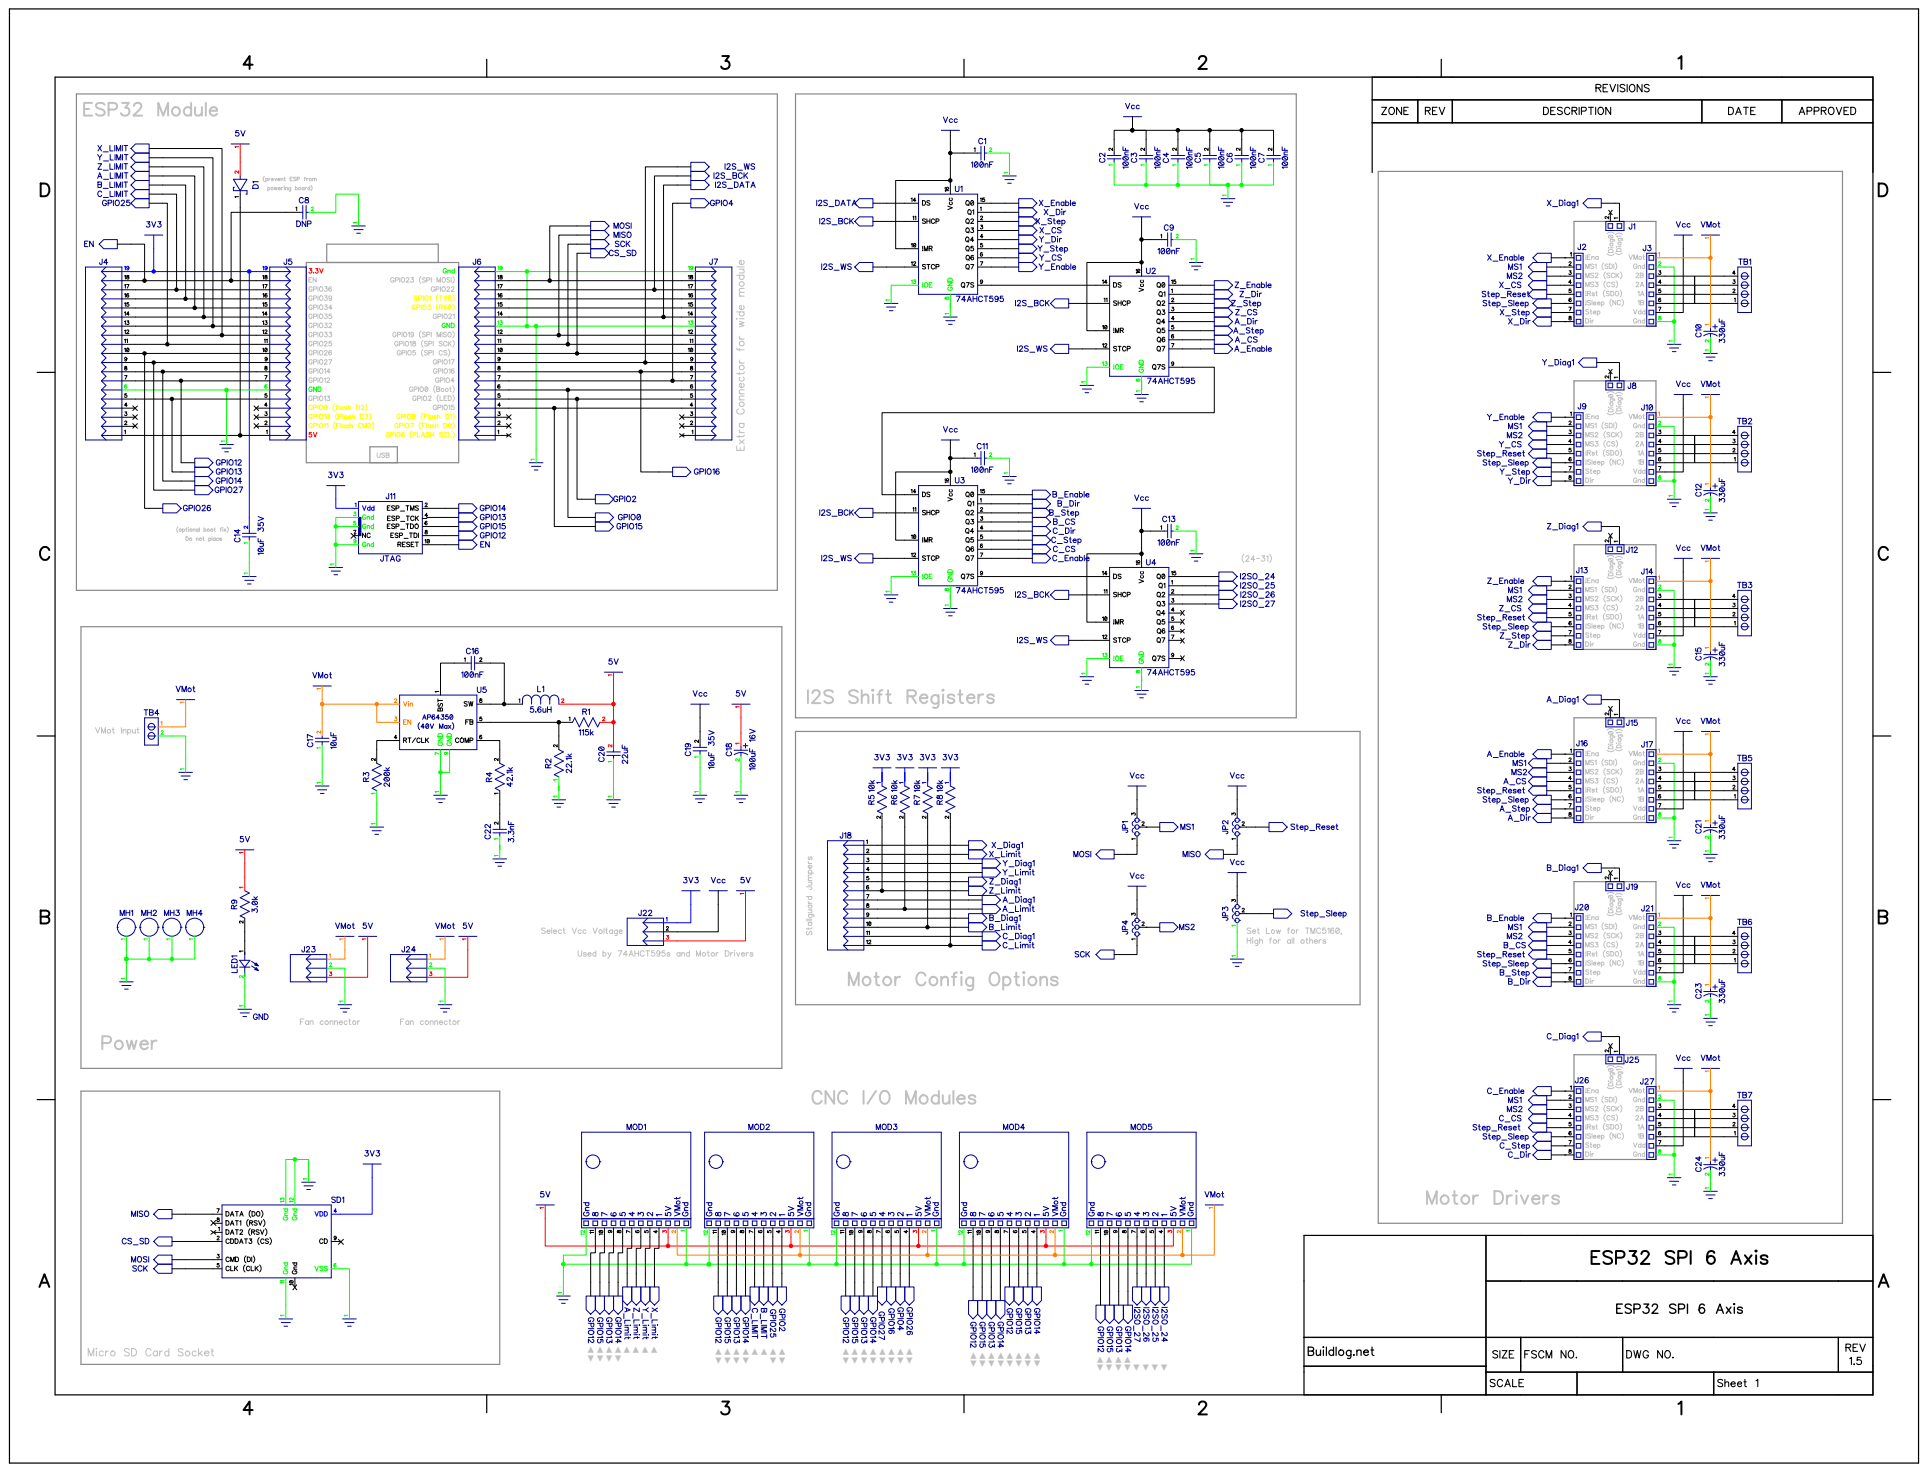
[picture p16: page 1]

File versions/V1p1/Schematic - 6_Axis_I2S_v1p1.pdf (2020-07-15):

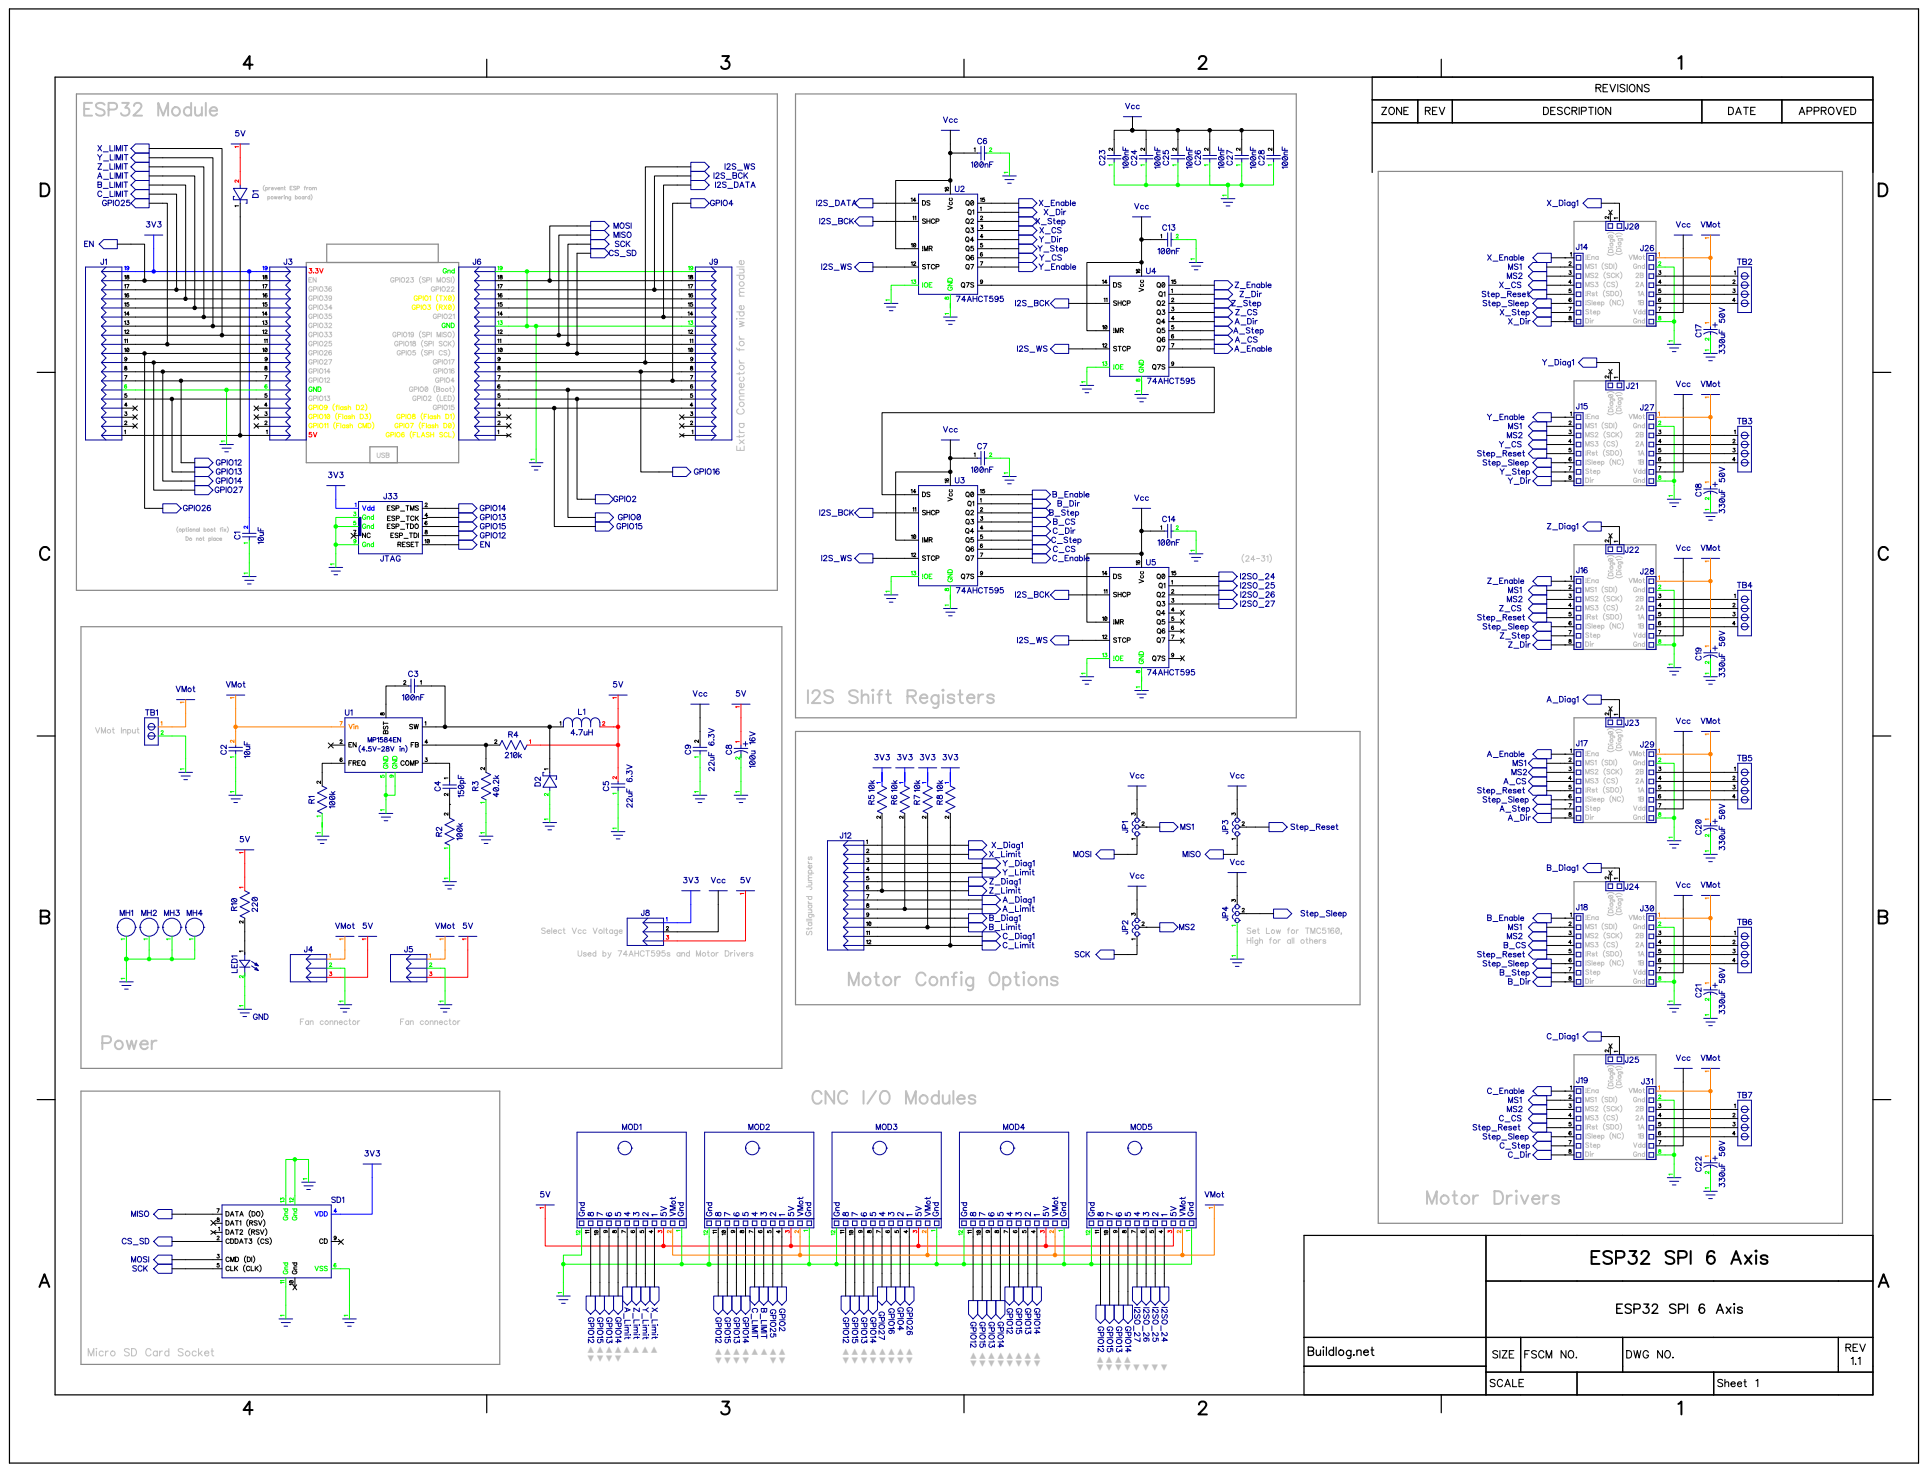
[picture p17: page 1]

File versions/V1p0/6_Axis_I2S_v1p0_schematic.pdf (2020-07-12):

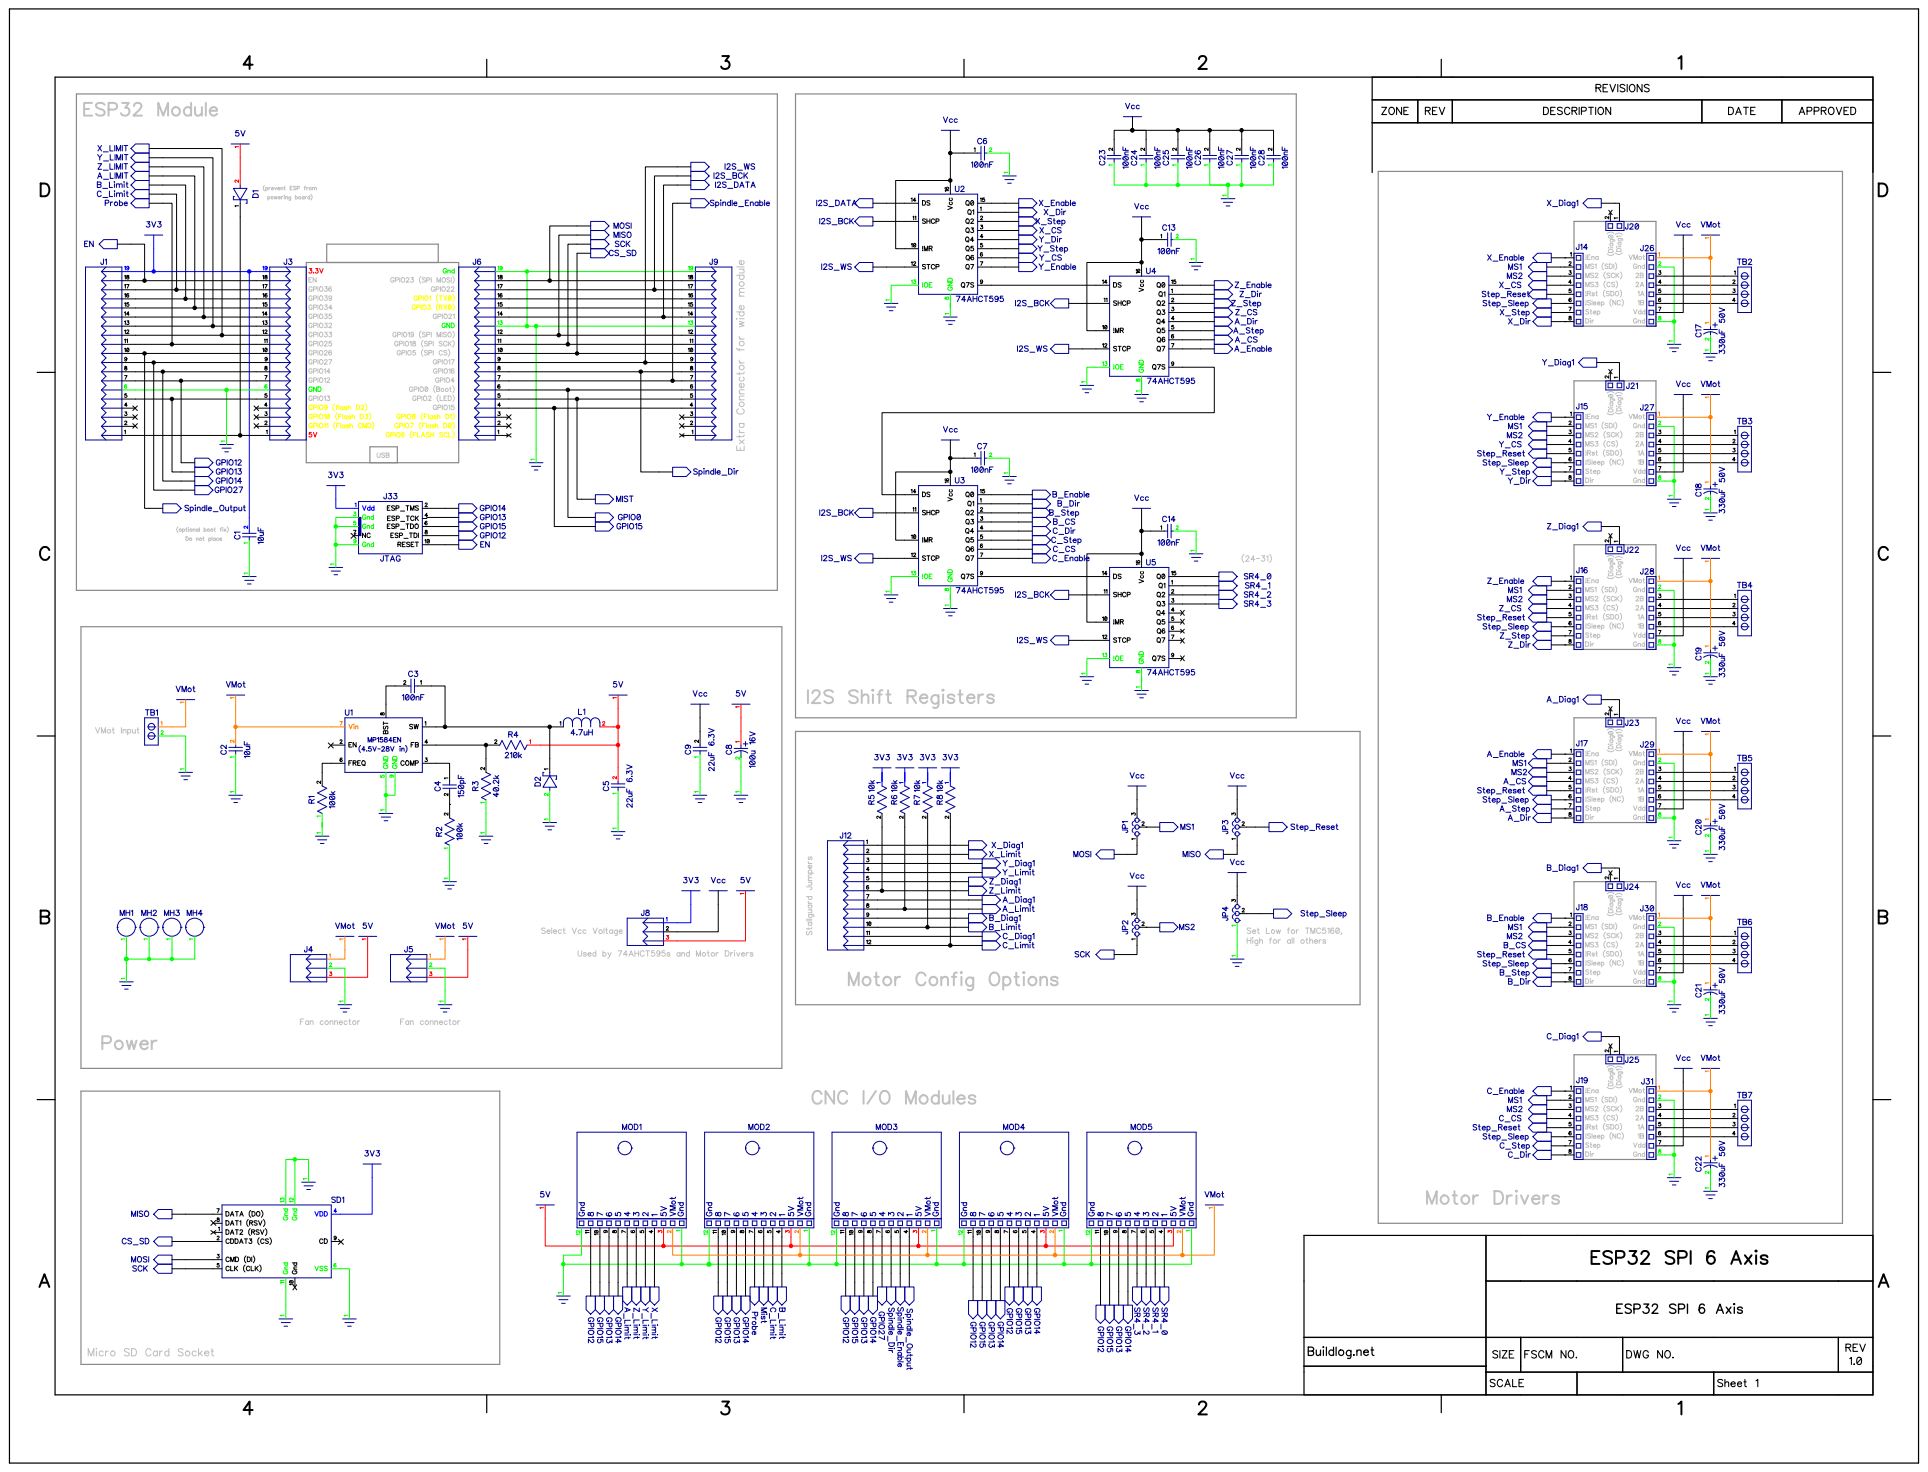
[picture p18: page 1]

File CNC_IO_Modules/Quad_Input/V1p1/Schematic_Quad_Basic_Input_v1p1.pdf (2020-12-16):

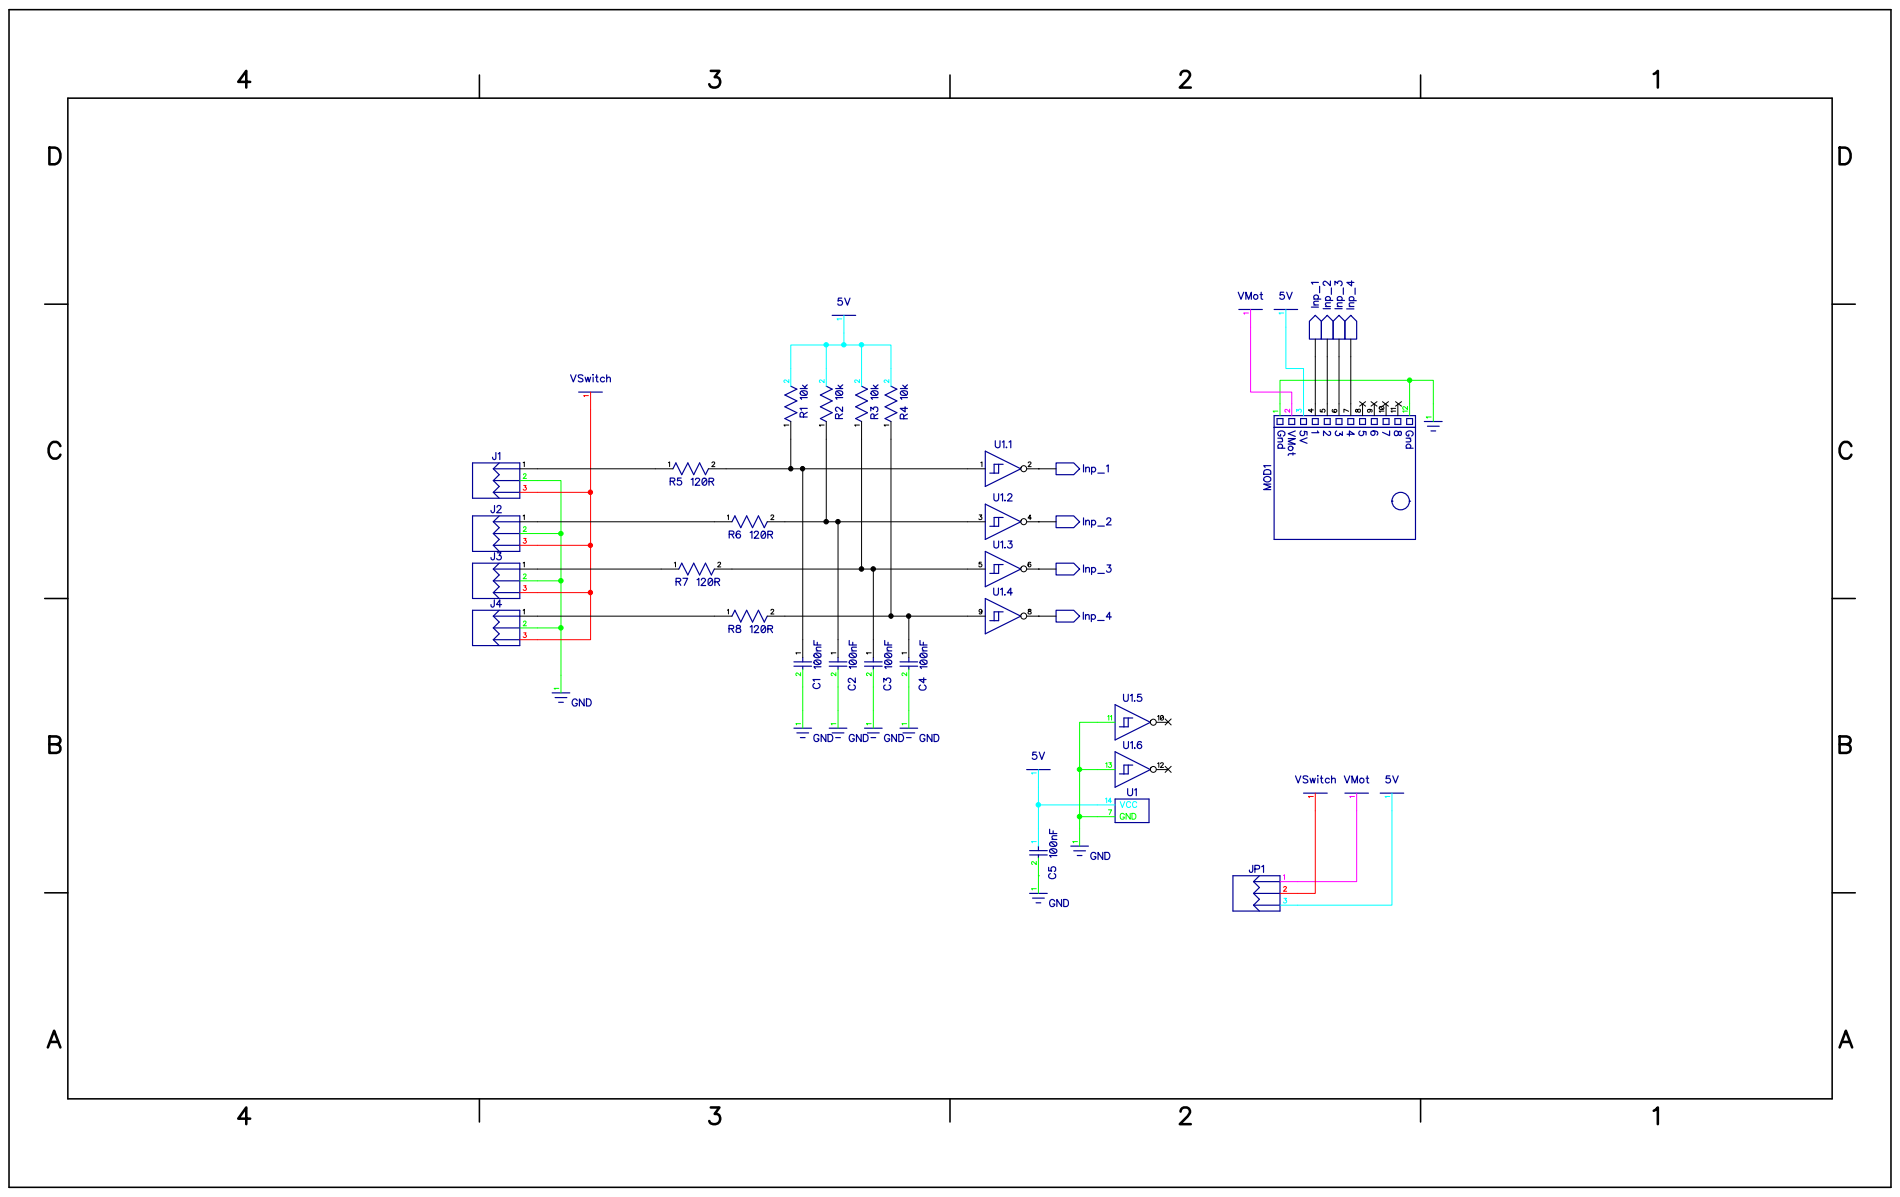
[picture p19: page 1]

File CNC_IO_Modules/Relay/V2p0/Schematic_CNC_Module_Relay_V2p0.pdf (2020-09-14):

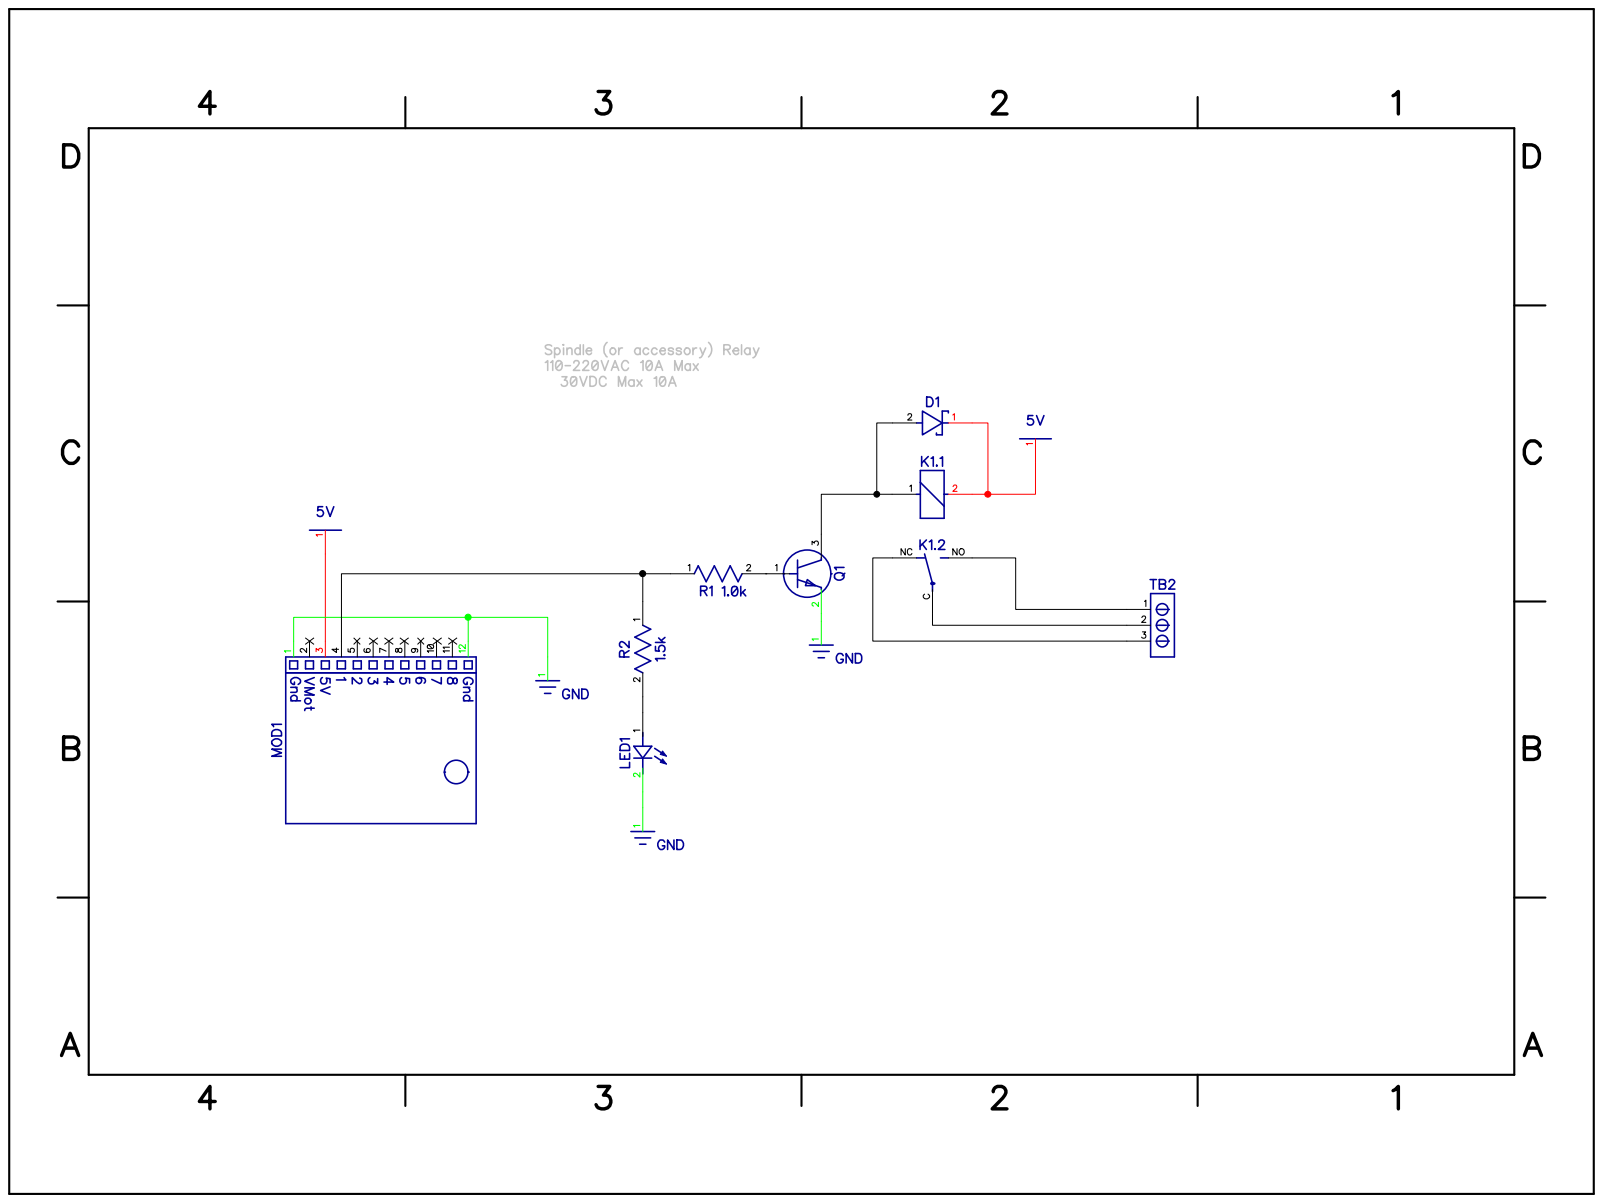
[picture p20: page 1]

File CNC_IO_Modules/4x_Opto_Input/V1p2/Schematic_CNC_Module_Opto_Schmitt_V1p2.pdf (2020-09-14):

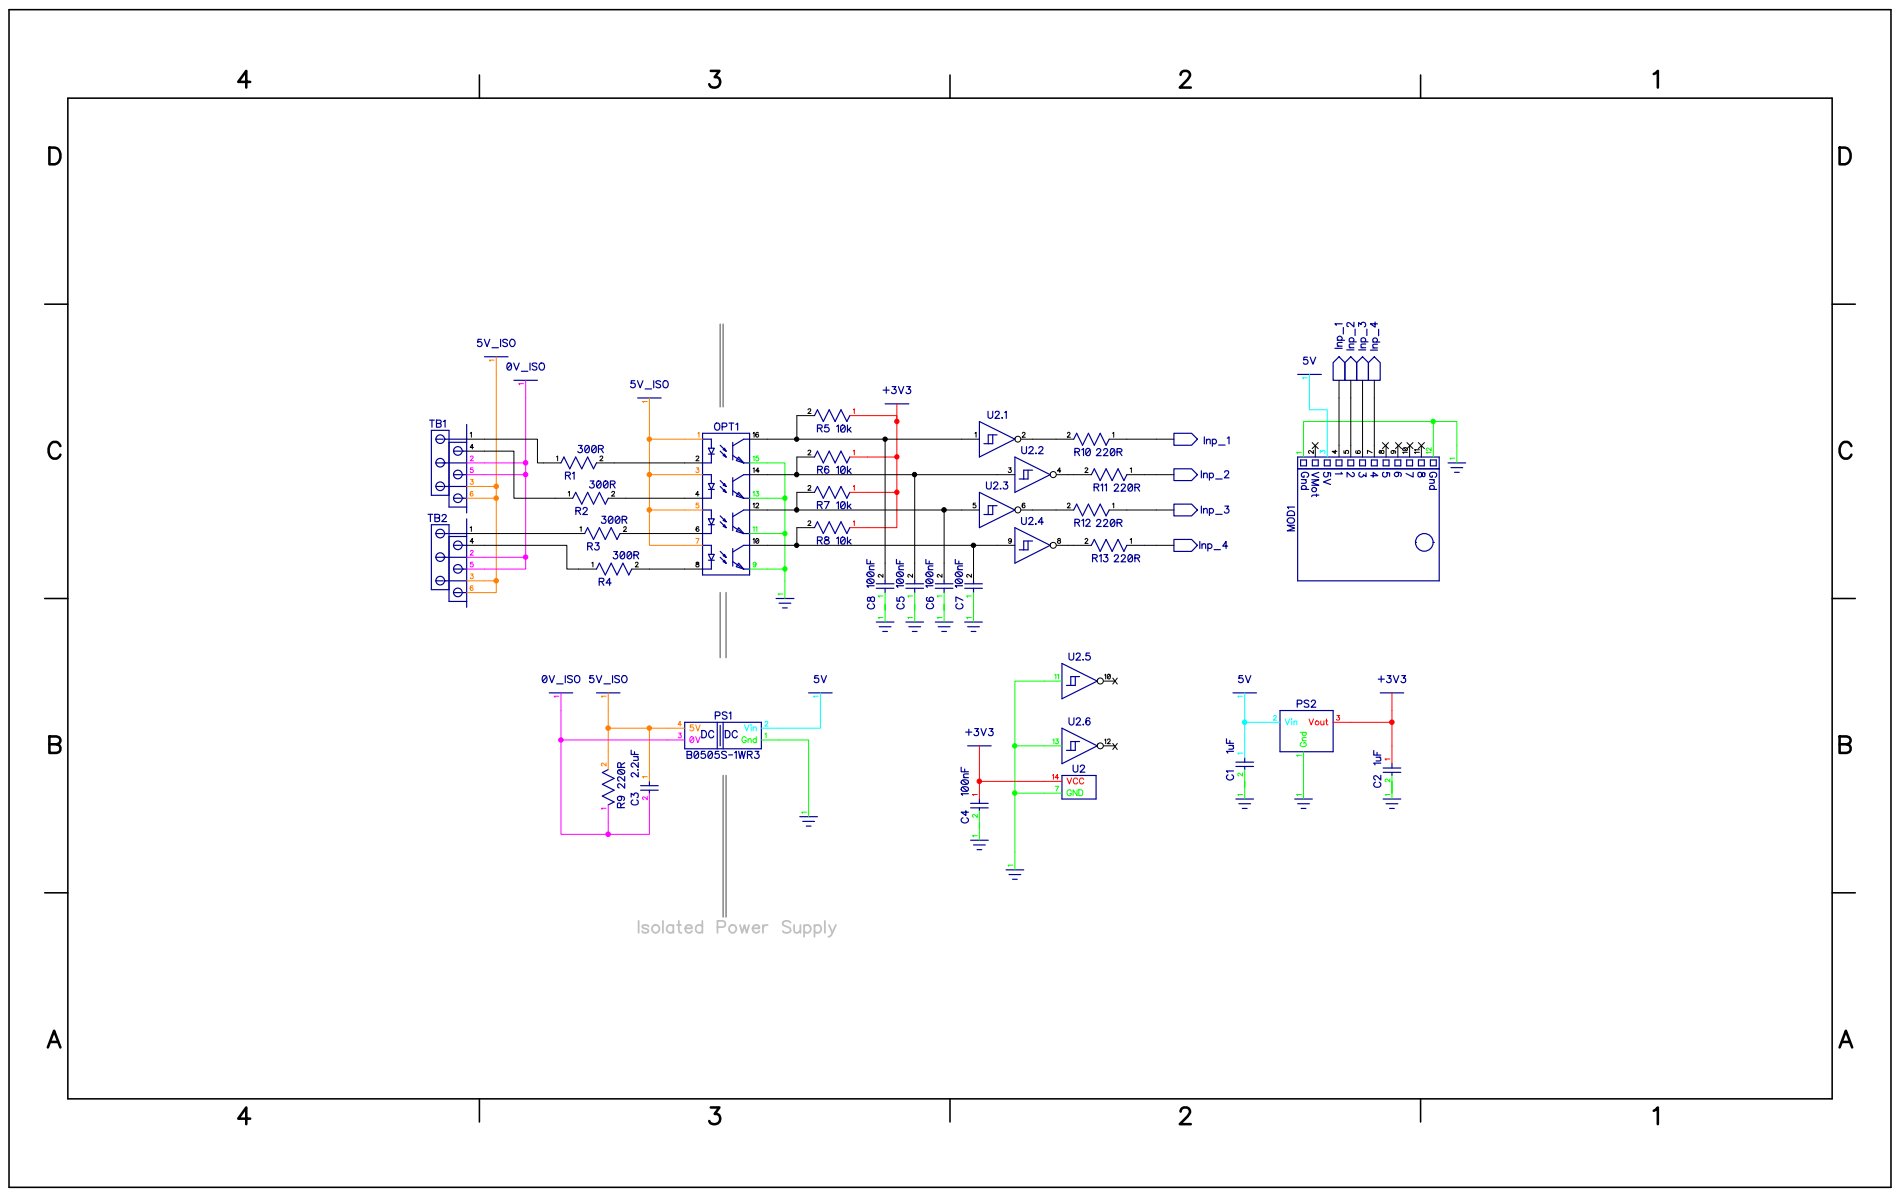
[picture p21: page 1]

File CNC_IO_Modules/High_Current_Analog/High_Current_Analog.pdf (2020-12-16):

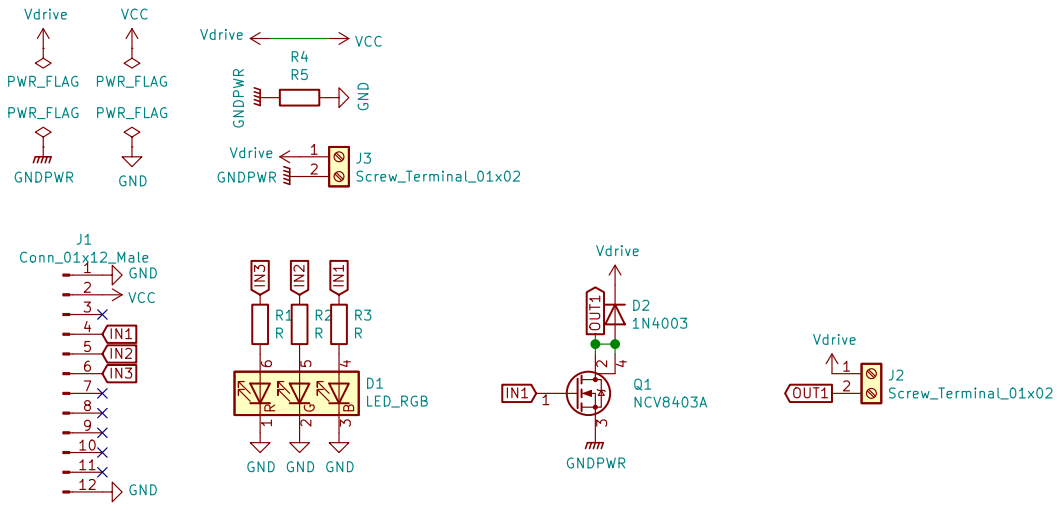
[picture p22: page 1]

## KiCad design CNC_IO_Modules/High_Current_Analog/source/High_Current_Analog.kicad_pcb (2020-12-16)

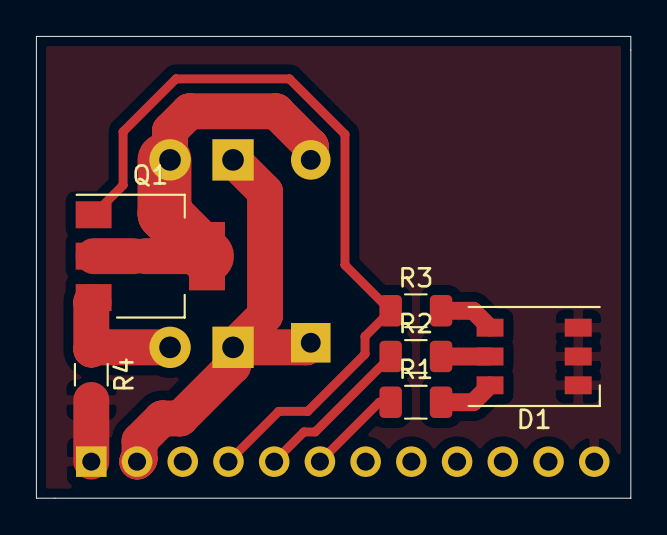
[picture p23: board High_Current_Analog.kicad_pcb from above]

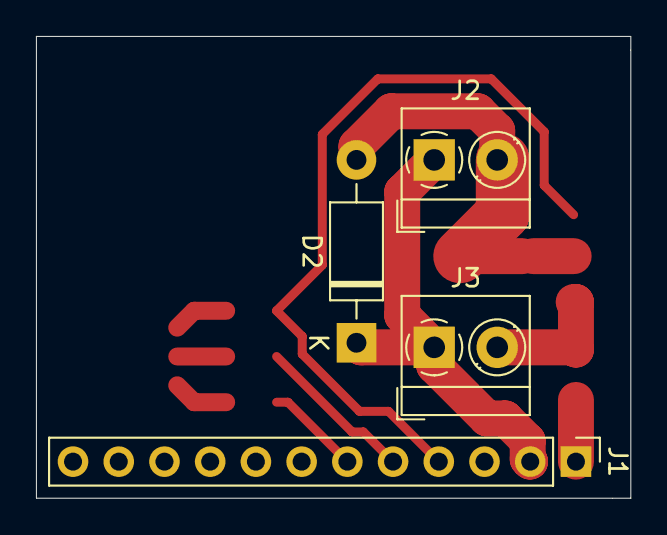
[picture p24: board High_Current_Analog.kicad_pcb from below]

Board: 2 copper layers, 33.0 x 25.7 mm, 10 parts (4 on the bottom side), 10 nets.

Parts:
D1: LED_RGB; LED_WS2812_PLCC6_5.0x5.0mm_P1.6mm
D2: 1N4003; D_DO-41_SOD81_P10.16mm_Horizontal
J1: Conn_01x12_Male; PinHeader_1x12_P2.54mm_Vertical
J2, J3: Screw_Terminal_01x02; TerminalBlock_MetzConnect_Type059_RT06302HBWC_1x02_P3.50mm_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
Q1: Q_NMOS_GDSD; SOT-223
R1, R2, R3, R4: R; R_1206_3216Metric

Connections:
GND: D1.1, D1.2, D1.3, J1.1, J1.12, R4.2
GNDPWR: J3.2, Q1.3, R4.1
IN1: J1.4, Q1.1, R3.1
IN2: J1.5, R2.1
IN3: J1.6, R1.1
unnamed: D1.4, R3.2
unnamed: D1.5, R2.2
unnamed: D1.6, R1.2
OUT1: D2.2, J2.2, Q1.2, Q1.4
VCC: D2.1, J1.2, J2.1, J3.1

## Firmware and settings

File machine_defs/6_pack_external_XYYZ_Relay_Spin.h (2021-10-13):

#pragma once
// clang-format off

/*
    6_pack_external_XXYZ_Relay_Spin.h

    Covers all V1 versions V1p0, V1p1, etc

    Part of Grbl_ESP32
    Pin assignments for the ESP32 I2S 6-axis board
   
    2021-09-20 B. Dring for Henry Thomas

    Grbl_ESP32 is free software: you can redistribute it and/or modify
    it under the terms of the GNU General Public License as published by
    the Free Software Foundation, either version 3 of the License, or
    (at your option) any later version.
    Grbl is distributed in the hope that it will be useful,
    but WITHOUT ANY WARRANTY; without even the implied warranty of
    MERCHANTABILITY or FITNESS FOR A PARTICULAR PURPOSE.  See the
    GNU General Public License for more details.
    You should have received a copy of the GNU General Public License
    along with Grbl_ESP32.  If not, see <http://www.gnu.org/licenses/>.
*/
#define MACHINE_NAME            "6 Pack External XYYZ"

#define N_AXIS 3

// === Special Features

// I2S (steppers & other output-only pins)
#define USE_I2S_OUT
#define USE_I2S_STEPS
//#define DEFAULT_STEPPER ST_I2S_STATIC


#define I2S_OUT_BCK             GPIO_NUM_22
#define I2S_OUT_WS              GPIO_NUM_17
#define I2S_OUT_DATA            GPIO_NUM_21

// Motor Socket #1
#define X_DISABLE_PIN           I2SO(0)
#define X_DIRECTION_PIN         I2SO(1)
#define X_STEP_PIN              I2SO(2)

// Motor Socket #2
#define Y_DIRECTION_PIN         I2SO(4)
#define Y_STEP_PIN              I2SO(5)
#define Y_STEPPER_MS3           I2SO(6)

// Motor Socket #3
#define Y2_DISABLE_PIN           I2SO(8)
#define Y2_DIRECTION_PIN         I2SO(9)
#define Y2_STEP_PIN              I2SO(10)

// Motor Socket #4
#define Z_DIRECTION_PIN         I2SO(12)
#define Z_STEP_PIN              I2SO(13)
#define Z_STEPPER_MS3           I2SO(14)

// // Motor Socket #5
// #define B_DISABLE_PIN           I2SO(16)
// #define B_DIRECTION_PIN         I2SO(17)
// #define B_STEP_PIN              I2SO(18)
// #define B_STEPPER_MS3           I2SO(19) 

// // Motor Socket #5
// #define C_DIRECTION_PIN         I2SO(20)
// #define C_STEP_PIN              I2SO(21)
// #define C_STEPPER_MS3           I2SO(22)
// #define C_DISABLE_PIN           I2SO(23)


/*
    Socket I/O reference
    The list of modules is here...
    https://github.com/bdring/6-Pack_CNC_Controller/wiki/CNC-I-O-Module-List
    Click on each module to get example for using the modules in the sockets

*/

// 4x Input Module in Socket #1
// https://github.com/bdring/6-Pack_CNC_Controller/wiki/4x-Switch-Input-module
#define X_LIMIT_PIN             GPIO_NUM_33
#define Y_LIMIT_PIN             GPIO_NUM_32
#define Z_LIMIT_PIN             GPIO_NUM_35
#define PROBE_PIN               GPIO_NUM_34


// Relay module as spindle on CNC I/O Module socket #3
// https://github.com/bdring/6-Pack_CNC_Controller/wiki/Relay-Module
#define SPINDLE_TYPE            SpindleType::RELAY // default, check actual $Spindle/Type Setting
#define SPINDLE_OUTPUT_PIN      GPIO_NUM_26 // relay as spindle on module socket #3

// === Default settings
// see wiki https://github.com/bdring/Grbl_Esp32/wiki/External-Stepper-Drivers
#define DEFAULT_STEP_ENABLE_DELAY        5 // how long after enable do we wait for 
#define DEFAULT_STEP_PULSE_MICROSECONDS  4 // length of step pulse. Must be greater than I2S_OUT_USEC_PER_PULSE (4) with I2S
#define STEP_PULSE_DELAY                 6 // gap between enable and dir changes before step

#define DEFAULT_INVERT_LIMIT_PINS       0  // Sets the default for N.O. switches

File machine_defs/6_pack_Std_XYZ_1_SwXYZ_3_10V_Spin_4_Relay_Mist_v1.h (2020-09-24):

#pragma once
// clang-format off

/*
    6_pack_Std_XYZ_1_SwXYZ_3_10V_Spin_4_Relay_Mist_v1.h

    Covers all V1 versions V1p0, V1p1, etc

    Part of Grbl_ESP32
    Pin assignments for the ESP32 I2S 6-axis board
    2018    - Bart Dring
    2020    - Mitch Bradley
    2020    - Michiyasu Odaki
    Grbl_ESP32 is free software: you can redistribute it and/or modify
    it under the terms of the GNU General Public License as published by
    the Free Software Foundation, either version 3 of the License, or
    (at your option) any later version.
    Grbl is distributed in the hope that it will be useful,
    but WITHOUT ANY WARRANTY; without even the implied warranty of
    MERCHANTABILITY or FITNESS FOR A PARTICULAR PURPOSE.  See the
    GNU General Public License for more details.
    You should have received a copy of the GNU General Public License
    along with Grbl_ESP32.  If not, see <http://www.gnu.org/licenses/>.
*/
#define MACHINE_NAME            "6 Pack Std XYZ 1_SwXYZ 3_10V_Spin 4_Relay_Mist"

#ifdef N_AXIS
        #undef N_AXIS
#endif
#define N_AXIS 3

#ifdef ENABLE_SD_CARD
    #undef ENABLE_SD_CARD
#endif

#ifdef HOMING_CYCLE_0
    #undef HOMING_CYCLE_0
#endif
#define HOMING_CYCLE_0 bit(Z_AXIS) // Z first

#ifdef HOMING_CYCLE_1
    #undef HOMING_CYCLE_1
#endif
#define HOMING_CYCLE_1 (bit(X_AXIS)|bit(Y_AXIS))

// === Special Features

// I2S (steppers & other output-only pins)
#define USE_I2S_OUT
#define USE_I2S_STEPS
//#define DEFAULT_STEPPER ST_I2S_STATIC
// === Default settings
#define DEFAULT_STEP_PULSE_MICROSECONDS I2S_OUT_USEC_PER_PULSE

#define USE_STEPSTICK   // makes sure MS1,2,3 !reset and !sleep are set

#define I2S_OUT_BCK      GPIO_NUM_22
#define I2S_OUT_WS       GPIO_NUM_17
#define I2S_OUT_DATA     GPIO_NUM_21

#define X_STEPPER_MS3           I2SO(3)   // X_CS
#define Y_STEPPER_MS3           I2SO(6)   // Y_CS
#define Z_STEPPER_MS3           I2SO(11)  // Z_CS

#define STEPPER_RESET           GPIO_NUM_19

#define X_DISABLE_PIN           I2SO(0)
#define X_DIRECTION_PIN         I2SO(1)
#define X_STEP_PIN              I2SO(2)

#define Y_DIRECTION_PIN         I2SO(4)
#define Y_STEP_PIN              I2SO(5)
#define Y_DISABLE_PIN           I2SO(7)

#define Z_DISABLE_PIN           I2SO(8)
#define Z_DIRECTION_PIN         I2SO(9)
#define Z_STEP_PIN              I2SO(10)


/*
    Socket I/O reference
    The list of modules is here...
    https://github.com/bdring/6-Pack_CNC_Controller/wiki/CNC-I-O-Module-List
    Click on each module to get example for using the modules in the sockets
*/

 
// Socket #1
// #1 GPIO_NUM_33 
// #2 GPIO_NUM_32
// #3 GPIO_NUM_35 (input only)
// #4 GPIO_NUM_34 (input only)


// Socket #2
// #1 GPIO_NUM_2
// #2 GPIO_NUM_25
// #3 GPIO_NUM_39 (input only)
// #4 GPIO_NUM_36 (input only)

// Socket #3
// #1 GPIO_NUM_26
// #2 GPIO_NUM_4
// #3 GPIO_NUM_16
// #4 GPIO_NUM_27


// Socket #4
// #1 GPIO_NUM_14
// #2 GPIO_NUM_13
// #3 GPIO_NUM_15
// #4 GPIO_NUM_12


// Socket #5
// #1 GPIO_NUM_24  (output only)
// #2 GPIO_NUM_25  (output only)
// #3 GPIO_NUM_26  (output only)
// #4 GPIO_NUM_27  (output only)

// Socket #1 Input
#define X_LIMIT_PIN             GPIO_NUM_33
#define Y_LIMIT_PIN             GPIO_NUM_32
#define Z_LIMIT_PIN             GPIO_NUM_35
#define PROBE_PIN               GPIO_NUM_34

// when used in socket #3
#define SPINDLE_TYPE            SpindleType::_10V
#define SPINDLE_OUTPUT_PIN      GPIO_NUM_26
#define SPINDLE_FORWARD_PIN     GPIO_NUM_4
#define SPINDLE_REVERSE_PIN     GPIO_NUM_16

// Relay module as Mist on CNC I/O Module socket #4
#define COOLANT_MIST_PIN  GPIO_NUM_14 // Relay for Mist on module socket #4

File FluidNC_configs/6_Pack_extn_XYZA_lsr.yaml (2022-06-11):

board: 6 Pack
name: 6 Pack External XYZA Laser
meta: 2022-01-06 B. Dring for Samuel Keller
stepping:
  engine: I2S_STREAM
  idle_ms: 250
  pulse_us: 4
  dir_delay_us: 1
  disable_delay_us: 0
  
kinematics:
  corexy:

axes:
  shared_stepper_disable_pin: NO_PIN
  x:
    steps_per_mm: 100.000
    max_rate_mm_per_min: 5000.000
    acceleration_mm_per_sec2: 50.000
    max_travel_mm: 300.000
    soft_limits: false
    homing:
      cycle: 1
      positive_direction: false
      mpos_mm: 0.000
      feed_mm_per_min: 100.000
      seek_mm_per_min: 200.000
      settle_ms: 500
      seek_scaler: 1.100
      feed_scaler: 1.100

    motor0:
      limit_neg_pin: NO_PIN
      limit_pos_pin: NO_PIN
      limit_all_pin: NO_PIN
      hard_limits: false
      pulloff_mm:1.000
      standard_stepper:
        step_pin: I2SO.2
        direction_pin: I2SO.1
        disable_pin: I2SO.0

  y:
    steps_per_mm: 100.000
    max_rate_mm_per_min: 5000.000
    acceleration_mm_per_sec2: 50.000
    max_travel_mm: 300.000
    soft_limits: false
    homing:
      cycle: 2
      positive_direction: true
      mpos_mm: 0.000
      feed_mm_per_min: 100.000
      seek_mm_per_min: 200.000
      settle_ms: 500
      seek_scaler: 1.100
      feed_scaler: 1.100

    motor0:
      limit_neg_pin: NO_PIN
      limit_pos_pin: NO_PIN
      limit_all_pin: NO_PIN
      hard_limits: false
      pulloff_mm:1.000
      standard_stepper:
        step_pin: I2SO.5
        direction_pin: I2SO.4
        disable_pin: I2SO.7
        
  z:
    steps_per_mm: 100.000
    max_rate_mm_per_min: 5000.000
    acceleration_mm_per_sec2: 200.000
    max_travel_mm: 1000.000
    soft_limits: false
    homing:
      cycle: 0
      positive_direction: true
      mpos_mm: 0.000
      feed_mm_per_min: 100.000
      seek_mm_per_min: 200.000
      settle_ms: 500
      seek_scaler: 1.100
      feed_scaler: 1.100
        
    motor0:
      limit_neg_pin: NO_PIN
      limit_pos_pin: NO_PIN
      limit_all_pin: NO_PIN
      hard_limits: false
      pulloff_mm:1.000
      null_motor:
        
  a:
    steps_per_mm: 100.000
    max_rate_mm_per_min: 5000.000
    acceleration_mm_per_sec2: 50.000
    max_travel_mm: 300.000
    soft_limits: false
    homing:
      cycle: 3
      positive_direction: true
      mpos_mm: 0.000
      feed_mm_per_min: 100.000
      seek_mm_per_min: 200.000
      settle_ms: 500
      seek_scaler: 1.100
      feed_scaler: 1.100
        
    motor0:
      limit_neg_pin: NO_PIN
      limit_pos_pin: NO_PIN
      limit_all_pin: NO_PIN
      hard_limits: false
      pulloff_mm:1.000
      standard_stepper:
        step_pin: I2SO.10
        direction_pin: I2SO.9
        disable_pin: I2SO.8

i2so:
  bck_pin: gpio.22
  data_pin: gpio.21
  ws_pin: gpio.17

spi:
  miso_pin: gpio.19
  mosi_pin: gpio.23
  sck_pin: gpio.18

sdcard:
  card_detect_pin: NO_PIN
  cs_pin: gpio.5

Laser:
  pwm_hz: 5000
  output_pin: gpio.14
  enable_pin: gpio.13
  disable_with_s0: false
  s0_with_disable: true
  tool_num: 100
  speed_map: 0=0.000% 255=100.000%
  

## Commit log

2020-05-29 First Push
    [BoardOutline.gbr, Bottom.gbr, BottomMask.gbr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]
2020-06-27 Uploading V1p0
    [1 - Top.gbr, 2 - Bottom.gbr, BoardOutline.gbr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]
2020-06-27 moved schematic
2020-07-12 Added CNC I/O Modules
    [BOM CNC Module RS485 V1p1.xlsx, BOM_Input_Module_V1p1.xlsx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]
2020-07-12 Add relay module image
2020-07-14 Added version 1p1
    [BOM 6_Pack_V1p1.xlsx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]
2020-07-25 Updating modules and adding external driver adapter
    [BOM CNC Module 0_10V.xlsx, BOM CNC Module 5V Output V2.0.xlsx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]
2020-08-07 Adding 3D files for module supports.
    The modules are typically supported on the outside edge with a single 11mm threaded spacer. That works OK, but I designed 2 3D parts that provide a little extra support.
    [1x_supp.stl, 1x_supp.stp, 4x_support.stl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]
2020-08-10 Update 5V Output module
    - Fix some BOM issues
    [BOM CNC Module 5V Output V2.0.xlsx, BOM.csv]
2020-08-21 3D part and new machine def
    [6_pack_foot.stl]
2020-08-27 Added terminal blocks to BOM
    [BOM 6_Pack_V1p1.xlsx]
2020-09-14 Added V1p5 source files
    [BOM.csv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]
2020-09-14 Added v1p2 of opto input module
    [BOM.csv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]
2020-09-14 Added V2p0 of relay module
    [BOM.csv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]
2020-09-14 Added Quad Mosfet files
    [BOM.csv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]
2020-09-17 Adding more files
    [1 - Top.gbr, 2 - Bottom.gbr, BoardOutline.gbr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]
2020-09-29 Added case files
    [6_pack_case_bottom_1.stl, 6_pack_case_bottom_2.stl, 6_pack_cover_top.stl]
2020-10-04 Updates to case and machine defs
    [6_pack_cover_top.stl, dummy_module.stl]
2020-10-10 Added machine defs and RC Servo Module
    [BOM.csv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]
2020-12-14 Add a new module
    [High_Current_Analog-B_Mask.gbr, High_Current_Analog-Edge_Cuts.gbr, High_Current_Analog-F_Cu.gbr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]
2020-12-16 New module and machine defs
    [1 - Top.gbr, 2 - Bottom.gbr, BoardOutline.gbr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]
2021-04-02 Added version 1.8 files
    [6_Park_V1p8_BOM.xlsx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]
2021-04-02 added sd files
    [6_pack_case_bottom_3.stl, 6_pack_case_bottom_3.stp, 6_pack_cover_top_3.stl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]
2021-04-24 Adding files
    [BoardOutline.gbr, Bottom.gbr, BottomMask.gbr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]
2021-06-24 Update 6_pack_external_XYYZ_10vSpin_Mist_Flood_Relays.h
    Fix typo in Y@ disable
    [6_pack_external_XYYZ_10vSpin_Mist_Flood_Relays.h]
2021-06-28 Updating 3D files
    [1x_supp.stl, 1x_supp.stp, 4x_support.stl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]
2021-12-22 Adding configs
    [6_Pack_5160_XYYZ.yaml, 6_Pack_XY_Lathe_Huany.yaml, 6_Pack_stepstick_XYY.yaml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]
2022-03-22 Updated parts
    [6P_extn_XYZAB.yaml, 6P_extn_XYZ_10V.yaml, 6P_ss_Z_Relay.yaml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]
2022-04-28 adding cfgs
    [6P_2130_XYZ_Relay.yaml, 6P_extn_XYYZ.yaml, 6P_extn_XYYZ_10V_2.yaml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]
2022-06-11 config updates
    [6P_5160_XYZA_Relay.yaml, 6P_extn_XYYZ_10V_3.yaml, 6P_ss_XYZ.yaml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]
2022-11-14 update configs
    [6p_2130_XYYZA_laser.yaml]
2023-04-07 add configs
    [6P_5160_XYZA_MOSFET.yaml, 6_pack_ext_XYYZ_485.yaml]
2023-06-09 Adding config
    [6P_ss_XYZ_Huany.yaml, 6_pack_ext_XYYZ_Relay.yaml, 6_pack_ext_XYYZ_YL620.yaml]
